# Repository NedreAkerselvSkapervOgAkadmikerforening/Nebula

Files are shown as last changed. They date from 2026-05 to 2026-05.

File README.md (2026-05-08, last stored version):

# Nebula
## Introduksjon
Nebula er foreningen NASAs neste generasjons flydatamaskin til bruk i foreningens modellrakketter.

## 🎯 Mål
1. Nebula skal være rask, kompakt, pålitelig, effektiv og enkel i bruk.
2. Nebula skal være bygd modulært, så nye sensorer og systemer kan innbyttes.
3. Sensorene i Nebula skal være nøyaktige og pålitelige.

## 💽 Oppbygning
Nebula kan overordnet deles i to kategorier:
1. Hovedkort
2. Modulene

### 🏠 Hovedkortet
Hovedkortet er hjernen og master i hele flydatamaskinen. Kortet bruker primært SPI-protokoll til å kommunisere med modulene.

Systemet drives av et enkelt 3.7 V LiPo-batteri, med 3.3 V logikk for alle moduler.

**Sensorer:**
- BMP390 - Trykk- og temperatursensor ([lenke](https://www.3achips.com/p/11139403?utm_source=octopart&utm_medium=cpc&utm_campaign=3achips_launch))
- BNO086 - Akselerometer, gyroskop og magnetometer

**Datalogging:**
- MEM2067-02-180-00-A - Hengslet SD kort modul ([lenke](https://no.mouser.com/ProductDetail/GCT/MEM2067-02-180-00-A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))

**Telemetri:**
- SX1276 - LoRa transceiver for trådløs kommunikasjon med bakken

**Kommunikasjon:**
- USB-C (alternativt micro USB) – for kommunikasjon med PC og programmering

**Strømforsyning:**
- Voltage divider - For å måle spenningen på batteriet gjennom ADC på mikrokontrolleren
- TPS63020 - 3.3V spenningsregulator (VURDER)
- JST 2-pin - For å koble til batteriet
- Power switch - For å slå av og på hele systemet

**Debugging:**
- Power LED - For å indikere at systemet er på
- Status LED - For å indikere systemstatus (f.eks. feil, normal drift, etc.)

### 📨 SPI
Hovedkortet fungerer som master, modulene som slaves. Hver modul har egen CS‑pin, som kan velges ved å lodde over riktig solder pad (CS1–CS6).

Mikrokontrolleren har totalt fire SPI-busser. 2 reserveres til selve hovedkortet, og 2 til modulene.

### 🖇️ Konnektorer
I alle moduler skal det være en 20 pin konnektor som kobler modulen til hovedkortet. Denne skal ha følgende pinout:
- CS: 6 stk
- MISO: 2 stk
- MOSI: 2 stk
- SCK: 2 stk
- 3vO: 1 stk
- GND: 1 stk
- GPIO: 6 stk

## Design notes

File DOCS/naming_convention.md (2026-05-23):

# Naming convention for nebula
Disse retningslinjene er ment for å sikre konsistens mellom moduler i PCB-design.

# Generelt
### 🐍 Alt bruker snakecase
altså_at_man_skriver_sånn_her

# Netlabels
### 📄 Netlabels skal være i formatet:
[modul(eks: "BNO086")][funksjon(eks: "MISO")][tiltegnet pin på MCU(eks: "30")]

### Eksempel
BNO086_MISO_30

### ⚡ Power
Alle positive powersymbols skal være 3.3V.

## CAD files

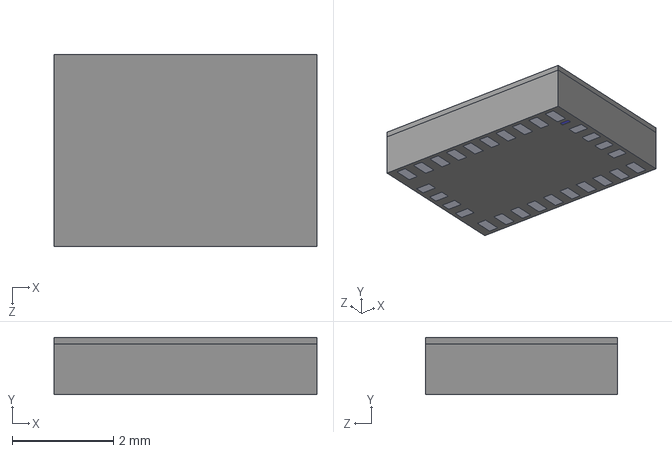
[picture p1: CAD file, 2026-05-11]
BNO086/DOCS/LIB_BNO086/BNO086/3D/BNO086.stp
5.20 x 1.13 x 3.80 mm

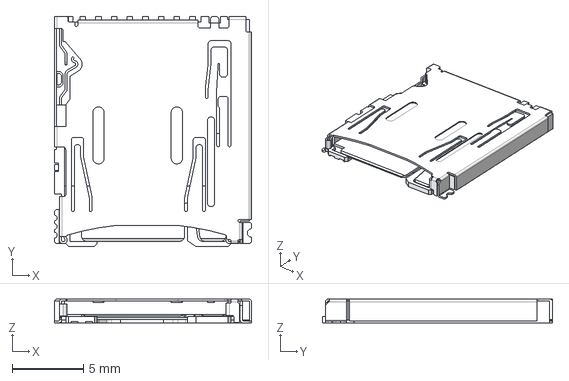
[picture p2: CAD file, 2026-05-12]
DM3AT/DM3AT_main/DM3AT-SF-PEJM5_40_.stp
13.8 x 16.2 x 1.68 mm

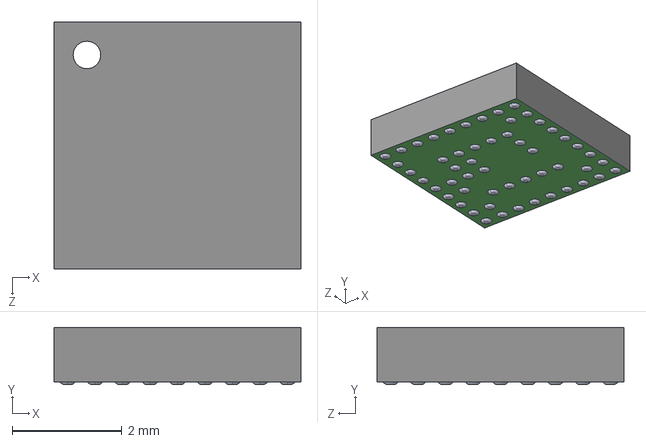
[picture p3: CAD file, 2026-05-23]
GPS pcb real/MIA-M10Q-00B feet/MIA-M10Q-00B.step
4.50 x 1.04 x 4.50 mm

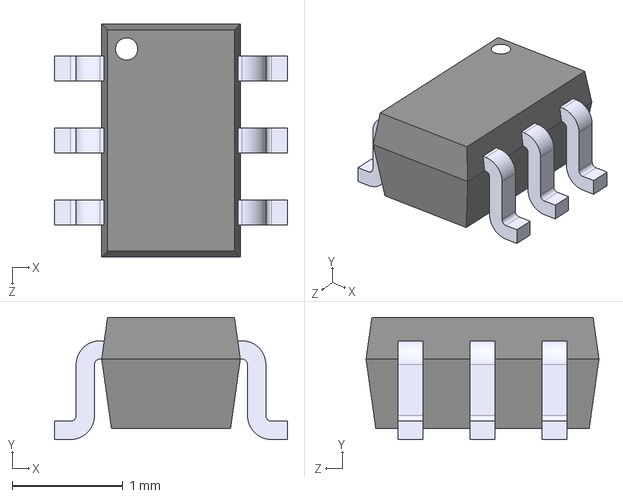
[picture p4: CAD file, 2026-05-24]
SX1276_Roy/PE4259/PE4259.step
2.10 x 1.10 x 2.10 mm

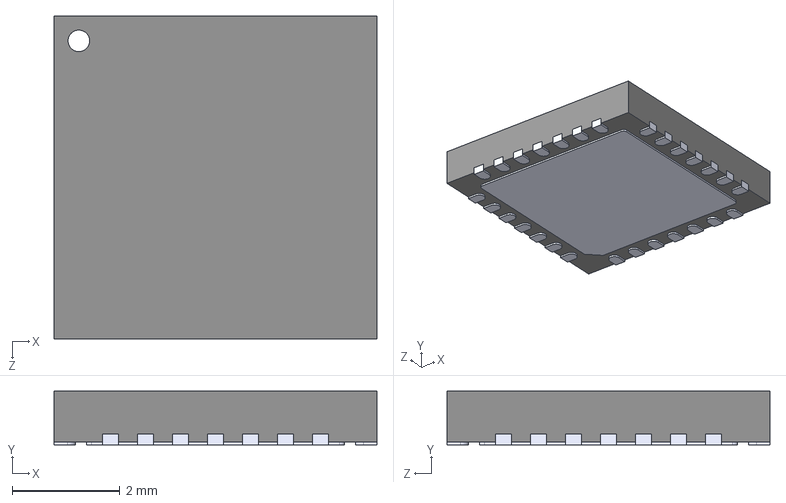
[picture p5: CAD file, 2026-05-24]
SX1276_Roy/SX1276IMLTRT/SX1276IMLTRT.step
6.00 x 1.00 x 6.00 mm

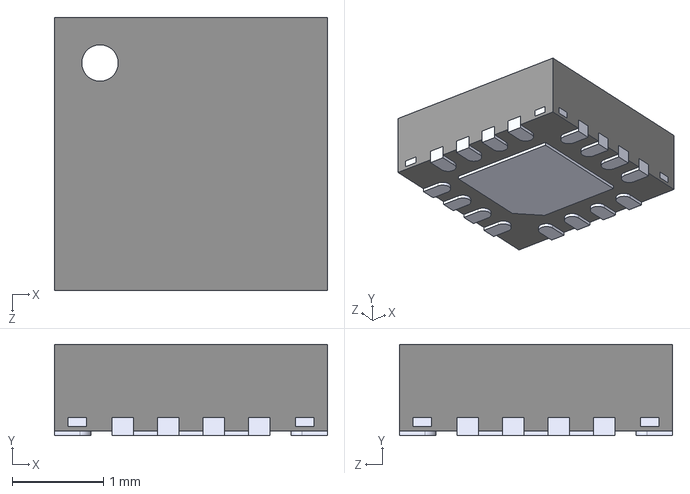
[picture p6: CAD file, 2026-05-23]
Batteri lader real/BQ24072RGTR feet/BQ24072RGTR.step
3.00 x 1.00 x 3.00 mm

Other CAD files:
BNO086/DOCS/LIB_BNO086/BNO086/Allegro/bno086.psm
BNO086/DOCS/LIB_BNO086/BNO086/DEHDL/bno086/chips/chips.prt

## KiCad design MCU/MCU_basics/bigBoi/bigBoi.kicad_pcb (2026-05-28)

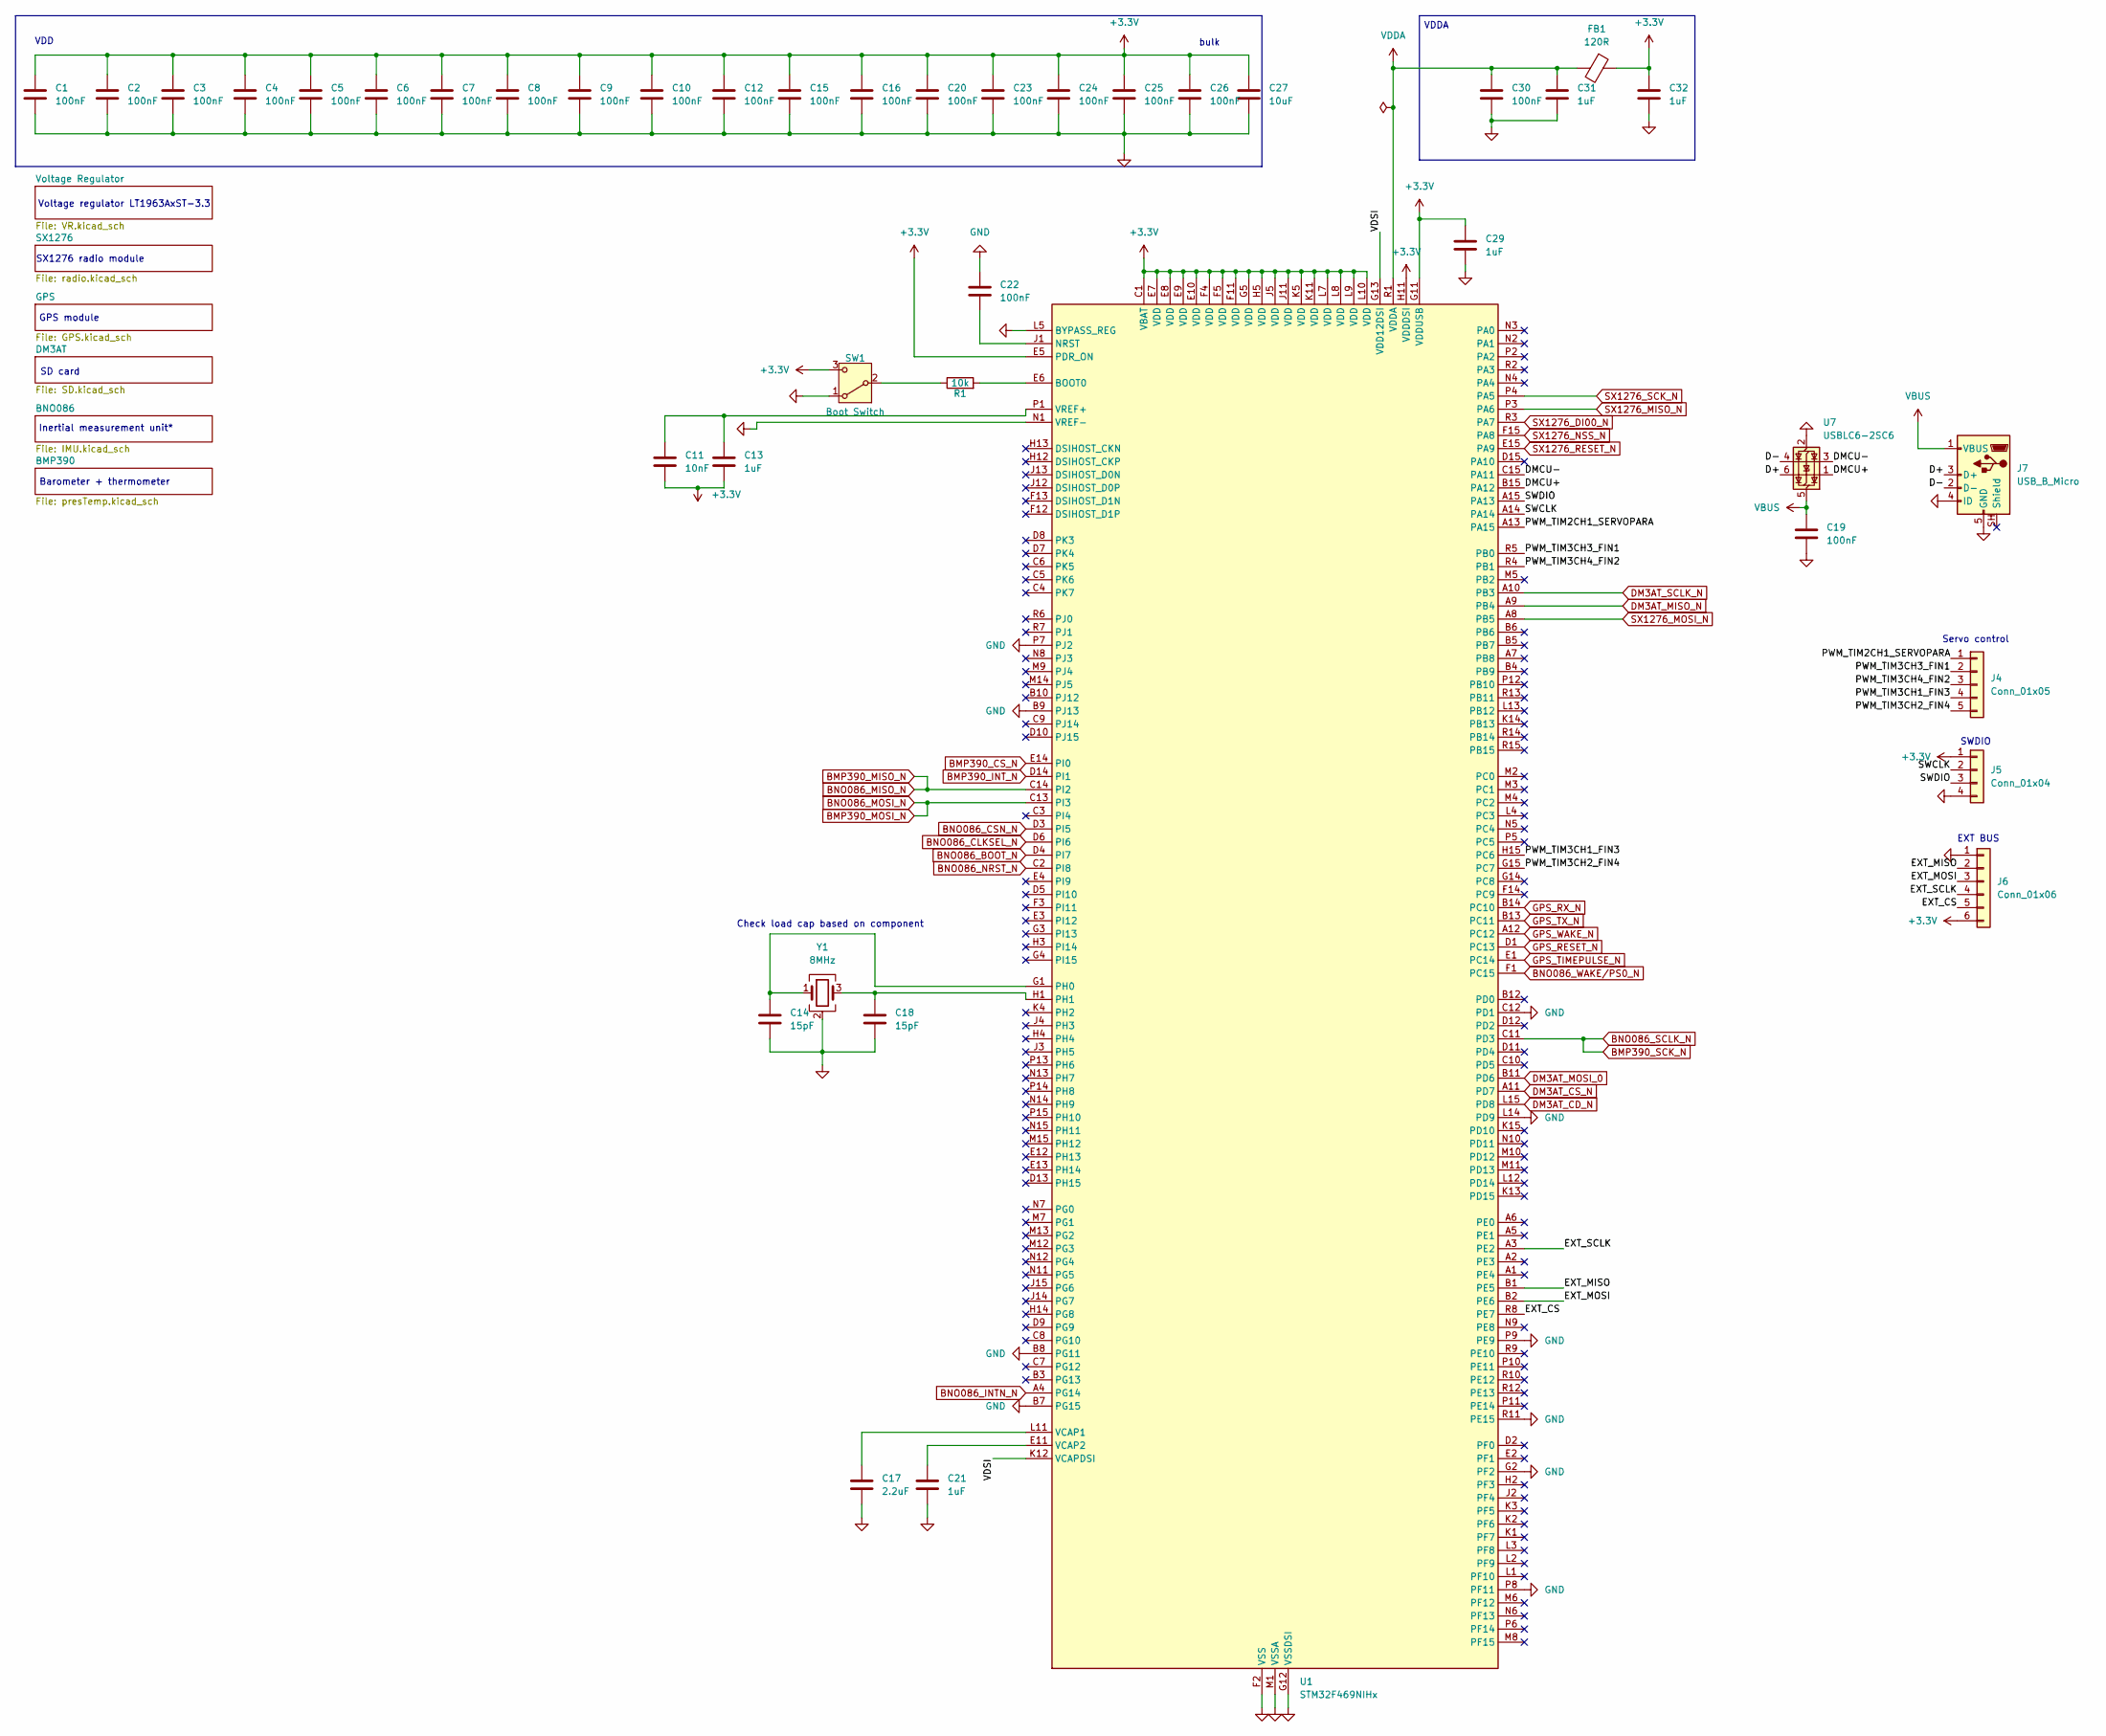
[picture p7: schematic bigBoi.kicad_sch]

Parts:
C1, C2, C3, C4, C5, C6, C7, C8, C9, C10, C12, C15, C16, C19, C20, C22, C23, C24, C25, C26, C30: 100nF; C_0402_1005Metric
C11: 10nF; C_0402_1005Metric
C13, C21, C29, C31, C32: 1uF; C_0402_1005Metric
C14, C18: 15pF; C_0402_1005Metric
C17: 2.2uF; C_0603_1608Metric
C27: 10uF; C_0805_2012Metric
FB1: 120R; L_0603_1608Metric
J4: Conn_01x05; PinHeader_1x05_P2.54mm_Vertical
J5: Conn_01x04; PinHeader_1x04_P2.54mm_Vertical
J6: Conn_01x06; PinHeader_1x06_P2.54mm_Vertical
J7: USB_B_Micro; USB_Micro-B_Molex_47346-0001
R1: 10k; R_0402_1005Metric
SW1: Boot Switch; SW_SPDT_PCM12
U1: STM32F469NIHx; TFBGA-216_13x13mm_Layout15x15_P0.8mm
U7: USBLC6-2SC6; SOT-23-6
Y1: 8MHz; Crystal_SMD_3225-4Pin_3.2x2.5mm

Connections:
+3.3V: C1.1, C2.1, C3.1, C4.1, C5.1, C6.1, C7.1, C8.1, C9.1, C10.1, C11.2, C12.1, C13.2, C15.1, C16.1, C20.1, C23.1, C24.1, C25.1, C26.1, C27.1, C29.1, C32.2, FB1.1, J5.1, J6.6, SW1.3 (C), U1.C1 (VBAT), U1.E5 (PDR_ON), U1.E7 (VDD), U1.E8 (VDD), U1.E9 (VDD), U1.E10 (VDD), U1.F4 (VDD), U1.F5 (VDD), U1.F11 (VDD), U1.G5 (VDD), U1.G11 (VDDUSB), U1.H5 (VDD), U1.H11 (VDDDSI), U1.J5 (VDD), U1.J11 (VDD), U1.K5 (VDD), U1.K11 (VDD), U1.L7 (VDD), U1.L8 (VDD), U1.L9 (VDD), U1.L10 (VDD); also elsewhere on the board
/D+: J7.3 (D+), U7.6 (I/O1)
/D-: J7.2 (D-), U7.4 (I/O2)
/DMCU+: U1.B15 (PA12), U7.1 (I/O1)
/DMCU-: U1.C15 (PA11), U7.3 (I/O2)
/EXT_CS: J6.5, U1.R8 (PE7)
/EXT_MISO: J6.2, U1.B1 (PE5)
/EXT_MOSI: J6.3, U1.B2 (PE6)
/EXT_SCLK: J6.4, U1.A3 (PE2)
/PWM_TIM2CH1_SERVOPARA: J4.1, U1.A13 (PA15)
/PWM_TIM3CH1_FIN3: J4.4, U1.H15 (PC6)
/PWM_TIM3CH2_FIN4: J4.5, U1.G15 (PC7)
/PWM_TIM3CH3_FIN1: J4.2, U1.R5 (PB0)
/PWM_TIM3CH4_FIN2: J4.3, U1.R4 (PB1)
/SWCLK: J5.2, U1.A14
/SWDIO: J5.3, U1.A15 (PA13)
/VDSI: U1.G13 (VDD12DSI), U1.K12 (VCAPDSI)
BMP390_CS_N: U1.E14 (PI0); also elsewhere on the board
BMP390_INT_N: U1.D14 (PI1); also elsewhere on the board
BMP390_MISO_N: U1.C14 (PI2); also elsewhere on the board
BMP390_MOSI_N: U1.C13 (PI3); also elsewhere on the board
BMP390_SCK_N: U1.C11 (PD3); also elsewhere on the board
BNO086_BOOT_N: U1.D4 (PI7); also elsewhere on the board
BNO086_CLKSEL_N: U1.D6 (PI6); also elsewhere on the board
BNO086_CSN_N: U1.D3 (PI5); also elsewhere on the board
BNO086_INTN_N: U1.A4 (PG14); also elsewhere on the board
BNO086_NRST_N: U1.C2 (PI8); also elsewhere on the board
BNO086_WAKE/PS0_N: U1.F1 (PC15); also elsewhere on the board
DM3AT_CD_N: U1.L15 (PD8); also elsewhere on the board
DM3AT_CS_N: U1.A11 (PD7); also elsewhere on the board
DM3AT_MISO_N: U1.A9 (PB4); also elsewhere on the board
DM3AT_MOSI_0: U1.B11 (PD6); also elsewhere on the board
DM3AT_SCLK_N: U1.A10 (PB3); also elsewhere on the board
GND: C1.2, C2.2, C3.2, C4.2, C5.2, C6.2, C7.2, C8.2, C9.2, C10.2, C12.2, C14.2, C15.2, C16.2, C17.2, C18.2, C19.2, C20.2, C21.1, C22.1, C23.2, C24.2, C25.2, C26.2, C27.2, C29.2, C30.1, C31.1, C32.1, J5.4, J6.1, J7.4 (ID), J7.5 (GND), SW1.1 (A), U1.B7 (PG15), U1.B8 (PG11), U1.B9 (PJ13), U1.C12 (PD1), U1.F2 (VSS), U1.F6 (VSS), U1.F7 (VSS), U1.F8 (VSS), U1.F9 (VSS), U1.F10 (VSS), U1.G2 (PF2), U1.G6 (VSS), U1.G10 (VSS), U1.G12 (VSSDSI), U1.H6 (VSS), U1.H10 (VSS), U1.J6 (VSS), U1.J10 (VSS), U1.K6 (VSS), U1.K7 (VSS), U1.K8 (VSS), U1.K9 (VSS), U1.K10 (VSS), U1.L5 (BYPASS_REG), U1.L6 (VSS), U1.L14 (PD9), U1.M1 (VSSA), U1.N1 (VREF-), U1.P7 (PJ2), U1.P8 (PF11), U1.P9 (PE9), U1.R11 (PE15), U7.2 (GND), Y1.2 (G), Y1.4 (G); also elsewhere on the board
GPS_RESET_N: U1.D1 (PC13); also elsewhere on the board
GPS_RX_N: U1.B14 (PC10); also elsewhere on the board
GPS_TIMEPULSE_N: U1.E1 (PC14); also elsewhere on the board
GPS_TX_N: U1.B13 (PC11); also elsewhere on the board
GPS_WAKE_N: U1.A12 (PC12); also elsewhere on the board
unnamed: R1.1, SW1.2 (B)
unnamed: R1.2, U1.E6 (BOOT0)
unnamed: C22.2, U1.J1 (NRST)
unnamed: C14.1, U1.G1 (PH0), Y1.1
unnamed: C18.1, U1.H1, Y1.3
unnamed: C17.1, U1.L11 (VCAP1)
unnamed: C21.2, U1.E11 (VCAP2)
unnamed: C11.1, C13.1, U1.P1 (VREF+)
SX1276_DI00_N: U1.R3 (PA7); also elsewhere on the board
SX1276_MISO_N: U1.P3 (PA6); also elsewhere on the board
SX1276_MOSI_N: U1.A8 (PB5); also elsewhere on the board
SX1276_NSS_N: U1.F15 (PA8); also elsewhere on the board
SX1276_RESET_N: U1.E15 (PA9); also elsewhere on the board
SX1276_SCK_N: U1.P4 (PA5); also elsewhere on the board
VBUS: C19.1, J7.1 (VBUS), U7.5 (VBUS); also elsewhere on the board
VDDA: C30.2, C31.2, FB1.2, U1.R1 (VDDA)

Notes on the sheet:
Inertial measurement unit*
bulk
VDD
EXT BUS
GPS module
SD card
VDDA
Voltage regulator LT1963AxST-3.3
Check load cap based on component
SX1276 radio module
Barometer + thermometer
SWDIO
Servo control

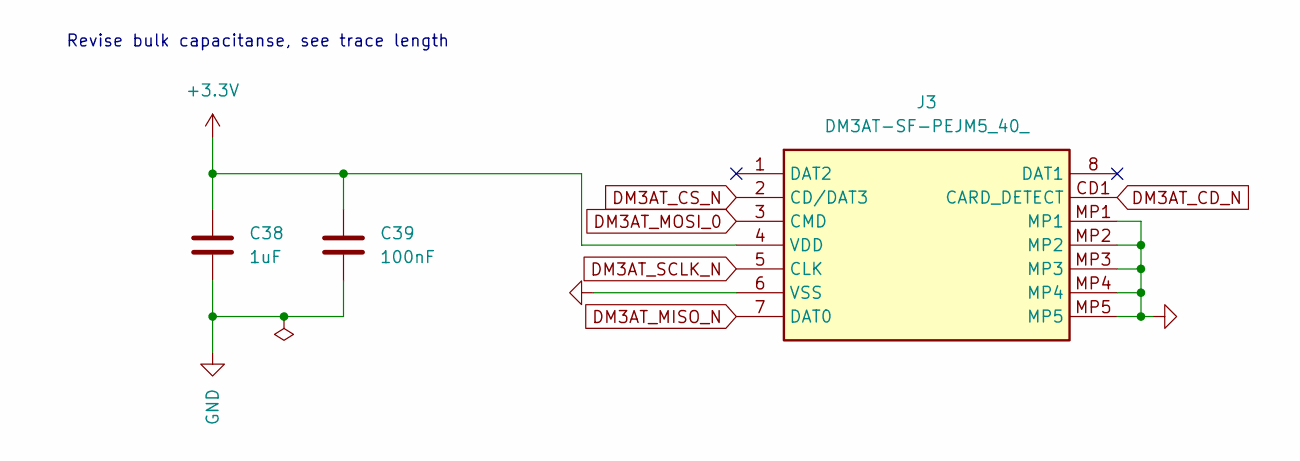
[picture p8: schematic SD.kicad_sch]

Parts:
C38: 1uF; C_0402_1005Metric
C39: 100nF; C_0402_1005Metric
J3: DM3AT-SF-PEJM5_40_; DM3ATSFPEJM540; Mouser Part Number 798-DM3AT-SF-PEJM540

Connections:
+3.3V: C38.1, C39.1, J3.4 (VDD); also elsewhere on the board
DM3AT_CD_N: J3.CD1 (CARD_DETECT); also elsewhere on the board
DM3AT_CS_N: J3.2 (CD/DAT3); also elsewhere on the board
DM3AT_MISO_N: J3.7 (DAT0); also elsewhere on the board
DM3AT_MOSI_0: J3.3 (CMD); also elsewhere on the board
DM3AT_SCLK_N: J3.5 (CLK); also elsewhere on the board
GND: C38.2, C39.2, J3.6 (VSS), J3.MP1, J3.MP2, J3.MP3, J3.MP4, J3.MP5; also elsewhere on the board

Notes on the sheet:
Revise bulk capacitanse, see trace length

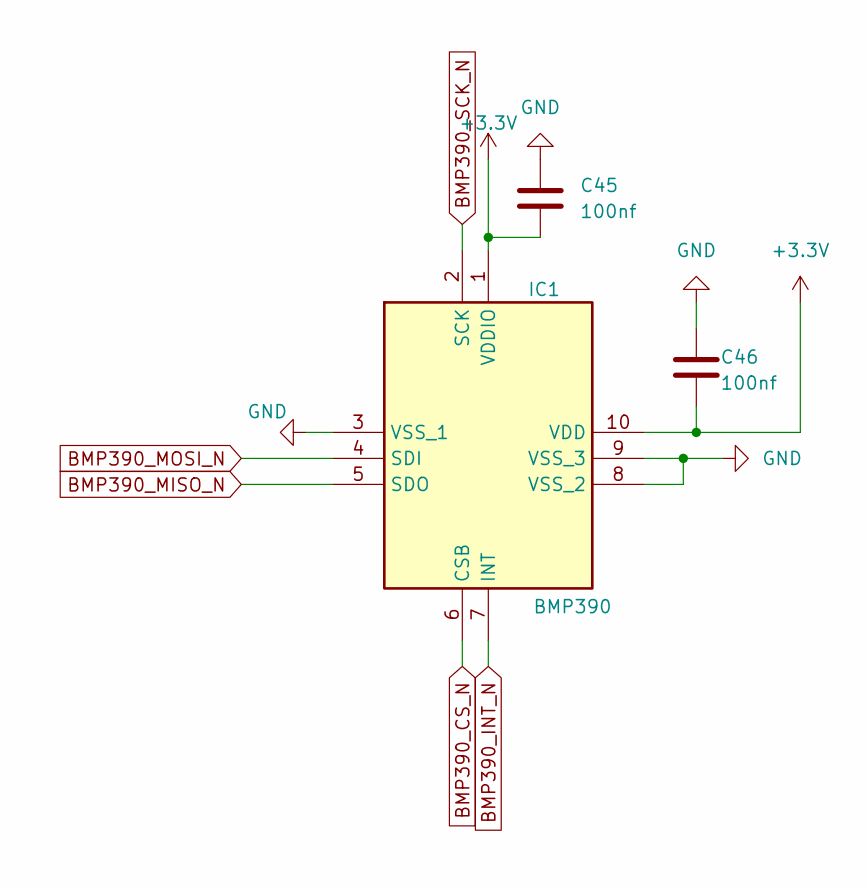
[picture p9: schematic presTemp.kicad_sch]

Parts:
C45, C46: 100nf; C_0402_1005Metric
IC1: BMP390; Manufacturer_Part_Number BMP390; Mouser Part Number 262-BMP390

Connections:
+3.3V: C45.2, C46.2, IC1.1 (VDDIO), IC1.10 (VDD); also elsewhere on the board
BMP390_CS_N: IC1.6 (CSB); also elsewhere on the board
BMP390_INT_N: IC1.7 (INT); also elsewhere on the board
BMP390_MISO_N: IC1.5 (SDO); also elsewhere on the board
BMP390_MOSI_N: IC1.4 (SDI); also elsewhere on the board
BMP390_SCK_N: IC1.2 (SCK); also elsewhere on the board
GND: C45.1, C46.1, IC1.3 (VSS_1), IC1.8 (VSS_2), IC1.9 (VSS_3); also elsewhere on the board

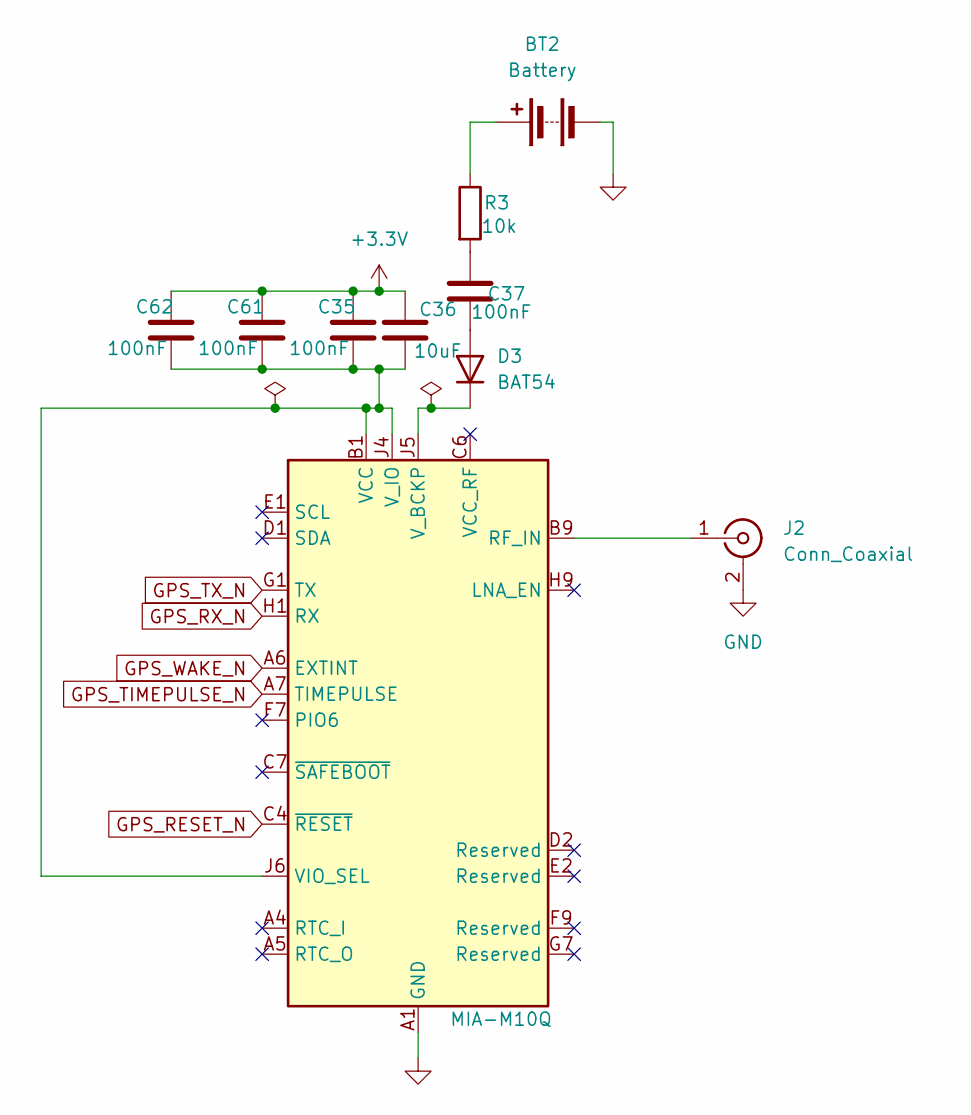
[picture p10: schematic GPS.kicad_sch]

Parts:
BT2: Battery; BatteryHolder_LINX_BAT-HLD-012-SMT
C35, C37, C61, C62: 100nF; C_0402_1005Metric
C36: 10uF; C_0603_1608Metric
D3: BAT54; D_0402_1005Metric
J2: Conn_Coaxial; U.FL_Hirose_U.FL-R-SMT-1_Vertical
R3: 10k; R_0402_1005Metric
U5: MIA-M10Q

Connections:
+3.3V: C35.1, C36.1, C61.1, C62.1; also elsewhere on the board
GND: BT2.2 (-), J2.2 (Ext), U5.A1 (GND), U5.A2 (GND), U5.A3 (GND), U5.A8 (GND), U5.A9 (GND), U5.B2 (GND), U5.B8 (GND), U5.C3 (GND), U5.C9 (GND), U5.E3 (GND), U5.E4 (GND), U5.E9 (GND), U5.F1 (GND), U5.F3 (GND), U5.F4 (GND), U5.G3 (GND), U5.G4 (GND), U5.G5 (GND), U5.G6 (GND), U5.H8 (GND), U5.J8 (GND), U5.J9 (GND); also elsewhere on the board
GPS_RESET_N: U5.C4 (~RESET); also elsewhere on the board
GPS_RX_N: U5.H1 (RX); also elsewhere on the board
GPS_TIMEPULSE_N: U5.A7 (TIMEPULSE); also elsewhere on the board
GPS_TX_N: U5.G1 (TX); also elsewhere on the board
GPS_WAKE_N: U5.A6 (EXTINT); also elsewhere on the board
unnamed: BT2.1 (+), R3.1
unnamed: C37.2, R3.2
unnamed: C37.1, D3.2 (A)
unnamed: D3.1 (K), U5.J5 (V_BCKP)
unnamed: J2.1 (In), U5.B9 (RF_IN)
unnamed: C35.2, C36.2, C61.2, C62.2, U5.B1 (VCC), U5.J4 (V_IO), U5.J6 (VIO_SEL)

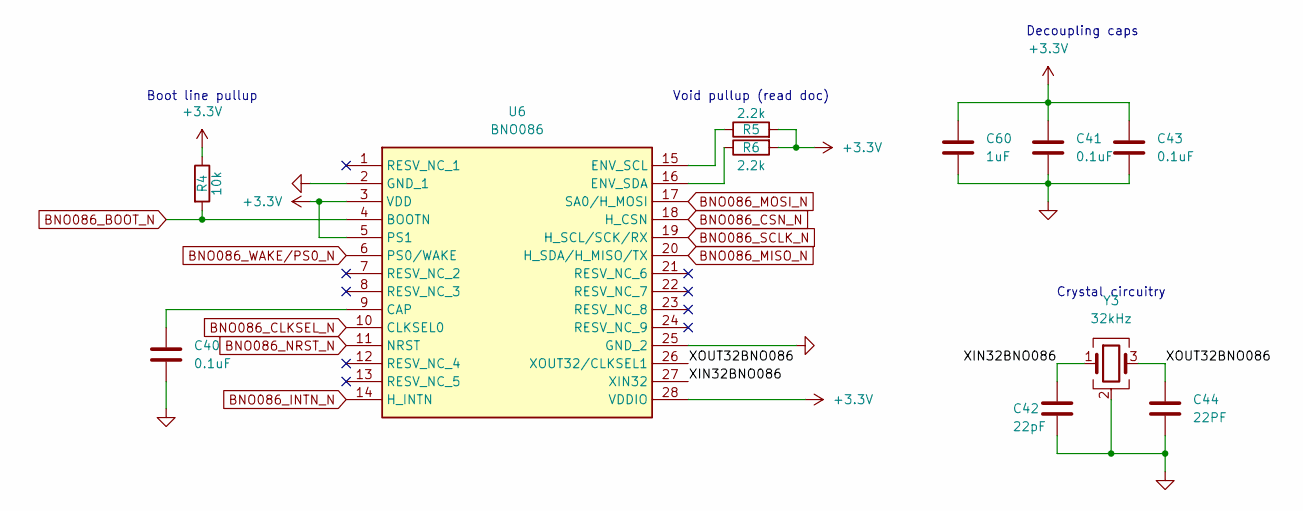
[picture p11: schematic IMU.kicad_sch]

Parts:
C40, C41, C43: 0.1uF; C_0402_1005Metric
C42: 22pF; C_0402_1005Metric
C44: 22PF; C_0402_1005Metric
C60: 1uF; C_0402_1005Metric
R4: 10k; R_0402_1005Metric
R5, R6: 2.2k; R_0402_1005Metric
U6: BNO086; Mouser Part Number 526-BNO086
Y3: 32kHz; Crystal_SMD_3225-4Pin_3.2x2.5mm

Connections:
+3.3V: C41.1, C43.1, C60.1, R4.1, R5.2, R6.2, U6.3 (VDD), U6.5 (PS1), U6.28 (VDDIO); also elsewhere on the board
/BNO086/XIN32BNO086: C42.1, U6.27 (XIN32), Y3.1
/BNO086/XOUT32BNO086: C44.1, U6.26 (XOUT32/CLKSEL1), Y3.3
BMP390_MISO_N: U6.20 (H_SDA/H_MISO/TX); also elsewhere on the board
BMP390_MOSI_N: U6.17 (SA0/H_MOSI); also elsewhere on the board
BMP390_SCK_N: U6.19 (H_SCL/SCK/RX); also elsewhere on the board
BNO086_BOOT_N: R4.2, U6.4 (BOOTN); also elsewhere on the board
BNO086_CLKSEL_N: U6.10 (CLKSEL0); also elsewhere on the board
BNO086_CSN_N: U6.18 (H_CSN); also elsewhere on the board
BNO086_INTN_N: U6.14 (H_INTN); also elsewhere on the board
BNO086_NRST_N: U6.11 (NRST); also elsewhere on the board
BNO086_WAKE/PS0_N: U6.6 (PS0/WAKE); also elsewhere on the board
GND: C40.2, C41.2, C42.2, C43.2, C44.2, C60.2, U6.2 (GND_1), U6.25 (GND_2), Y3.2 (G), Y3.4 (G); also elsewhere on the board
unnamed: C40.1, U6.9 (CAP)
unnamed: R5.1, U6.15 (ENV_SCL)
unnamed: R6.1, U6.16 (ENV_SDA)

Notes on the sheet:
Boot line pullup
Decoupling caps
Void pullup (read doc)
Crystal circuitry

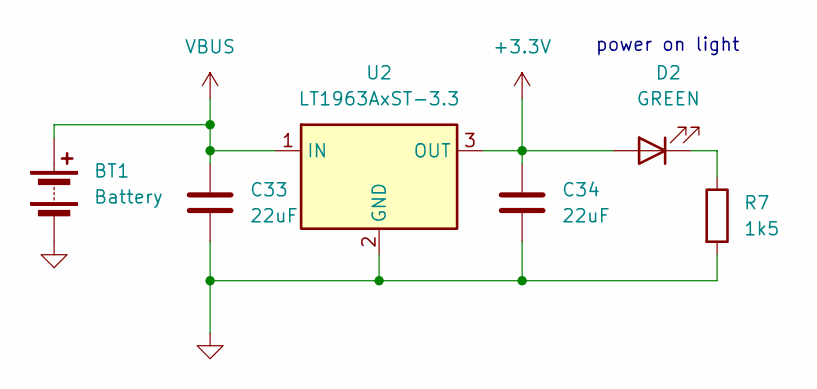
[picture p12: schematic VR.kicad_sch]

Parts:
BT1: Battery; JST_PH_S2B-PH-K_1x02_P2.00mm_Horizontal
C33, C34: 22uF; C_0805_2012Metric
D2: GREEN; LED_0603_1608Metric
R7: 1k5; R_0402_1005Metric
U2: LT1963AxST-3.3; SOT-223-3_TabPin2

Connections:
+3.3V: C34.1, D2.2 (A), U2.3 (OUT); also elsewhere on the board
GND: BT1.2 (-), C33.2, C34.2, R7.2, U2.2 (GND); also elsewhere on the board
unnamed: D2.1 (K), R7.1
VBUS: BT1.1 (+), C33.1, U2.1 (IN); also elsewhere on the board

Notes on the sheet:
power on light

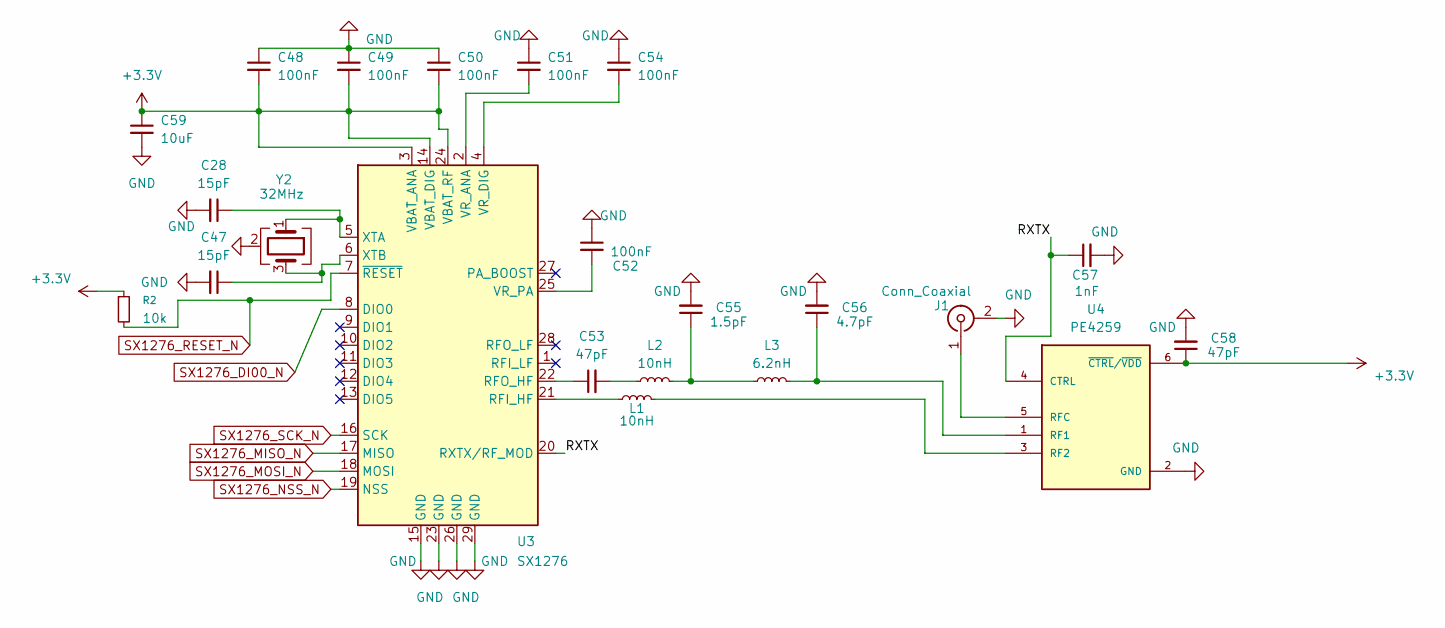
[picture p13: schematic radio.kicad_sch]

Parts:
C28, C47: 15pF; C_0402_1005Metric
C48, C49, C50, C51, C52, C54: 100nF; C_0402_1005Metric
C53, C58: 47pF; C_0402_1005Metric
C55: 1.5pF; C_0402_1005Metric
C56: 4.7pF; C_0402_1005Metric
C57: 1nF; C_0402_1005Metric
C59: 10uF; C_0805_2012Metric
J1: Conn_Coaxial; U.FL_Hirose_U.FL-R-SMT-1_Vertical
L1, L2: 10nH; L_0402_1005Metric
L3: 6.2nH; L_0402_1005Metric
R2: 10k; R_0402_1005Metric
U3: SX1276; QFN65P600X600X100-29N
U4: PE4259; SOT65P215X110-6N
Y2: 32MHz; Crystal_SMD_3225-4Pin_3.2x2.5mm

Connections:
+3.3V: C48.2, C49.2, C50.2, C58.1, C59.1, R2.1, U3.3 (VBAT_ANA), U3.14 (VBAT_DIG), U3.24 (VBAT_RF), U4.6 (~CTRL/~VDD); also elsewhere on the board
/SX1276/RXTX: C57.1, U3.20 (RXTX/RF_MOD), U4.4 (CTRL)
GND: C28.2, C47.2, C48.1, C49.1, C50.1, C51.1, C52.1, C54.1, C55.2, C56.2, C57.2, C58.2, C59.2, J1.2 (Ext), U3.15 (GND), U3.23 (GND), U3.26 (GND), U3.29 (GND), U4.2 (GND), Y2.2 (G), Y2.4 (G); also elsewhere on the board
unnamed: C53.2, L2.1
unnamed: C55.1, L2.2, L3.1
unnamed: J1.1 (In), U4.5 (RFC)
unnamed: L1.1, U3.21 (RFI_HF)
unnamed: C53.1, U3.22 (RFO_HF)
unnamed: C51.2, U3.2 (VR_ANA)
unnamed: C54.2, U3.4 (VR_DIG)
unnamed: C52.2, U3.25 (VR_PA)
unnamed: C28.1, U3.5 (XTA), Y2.1
unnamed: C47.1, U3.6 (XTB), Y2.3
unnamed: C56.1, L3.2, U4.1 (RF1)
unnamed: L1.2, U4.3 (RF2)
SX1276_DI00_N: U3.8 (DIO0); also elsewhere on the board
SX1276_MISO_N: U3.17 (MISO); also elsewhere on the board
SX1276_MOSI_N: U3.18 (MOSI); also elsewhere on the board
SX1276_NSS_N: U3.19 (NSS); also elsewhere on the board
SX1276_RESET_N: R2.2, U3.7 (~RESET); also elsewhere on the board
SX1276_SCK_N: U3.16 (SCK); also elsewhere on the board

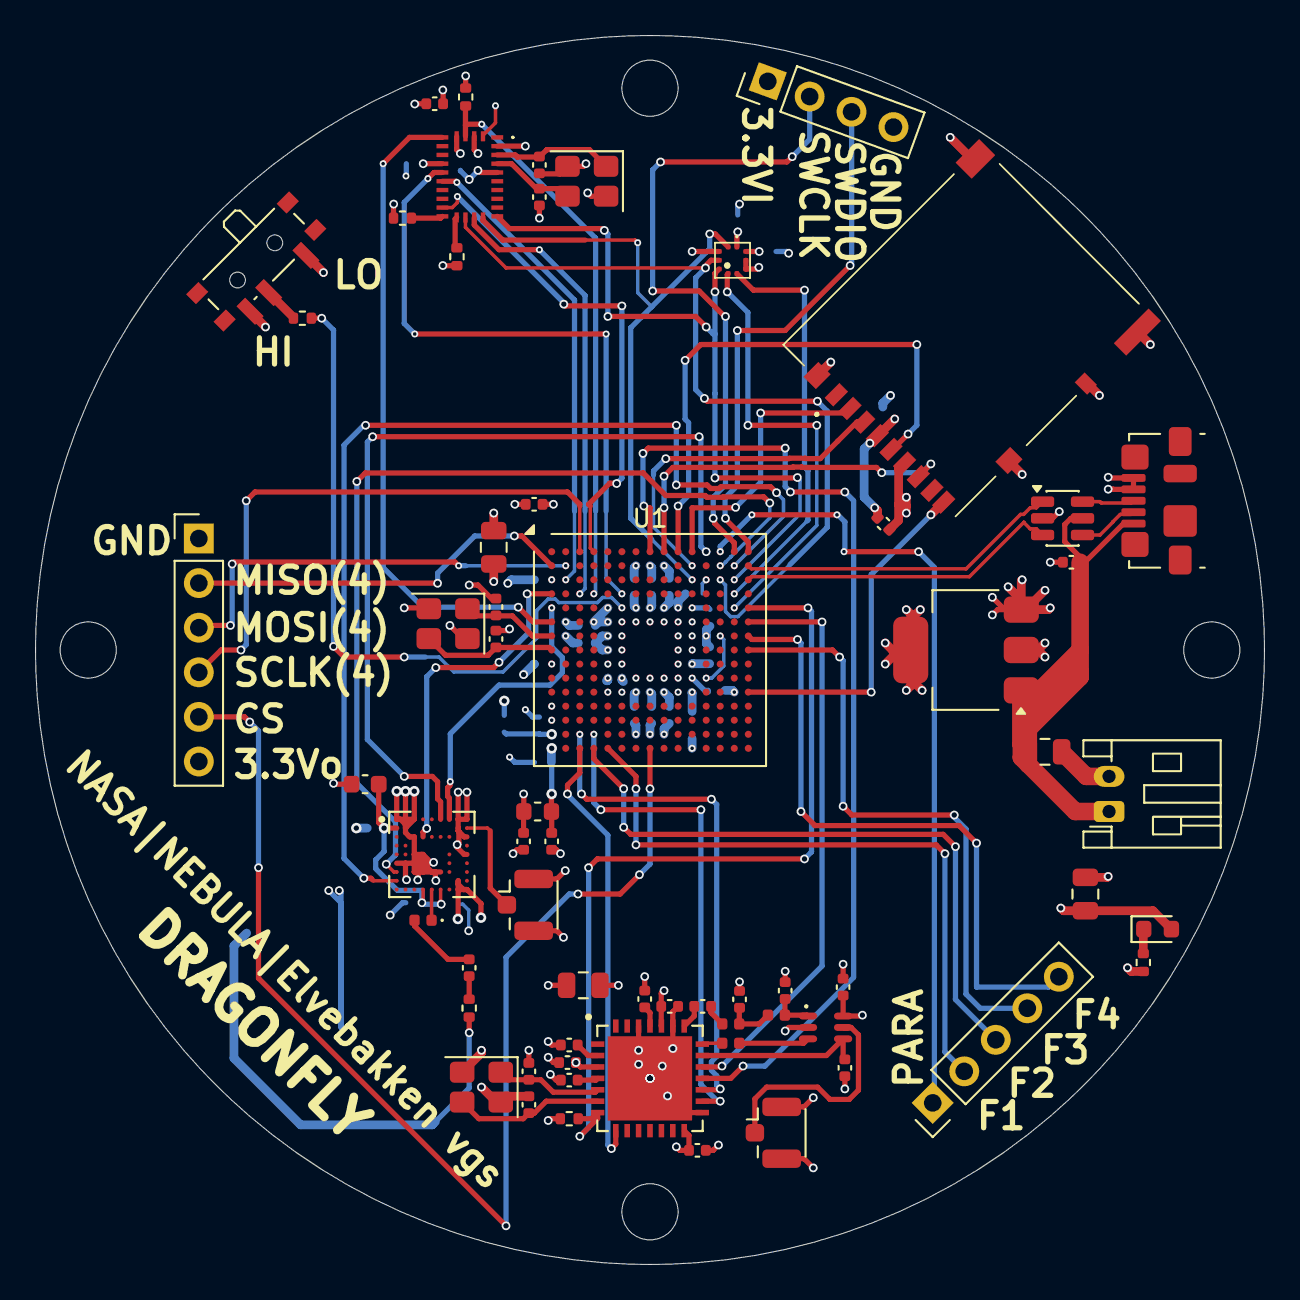
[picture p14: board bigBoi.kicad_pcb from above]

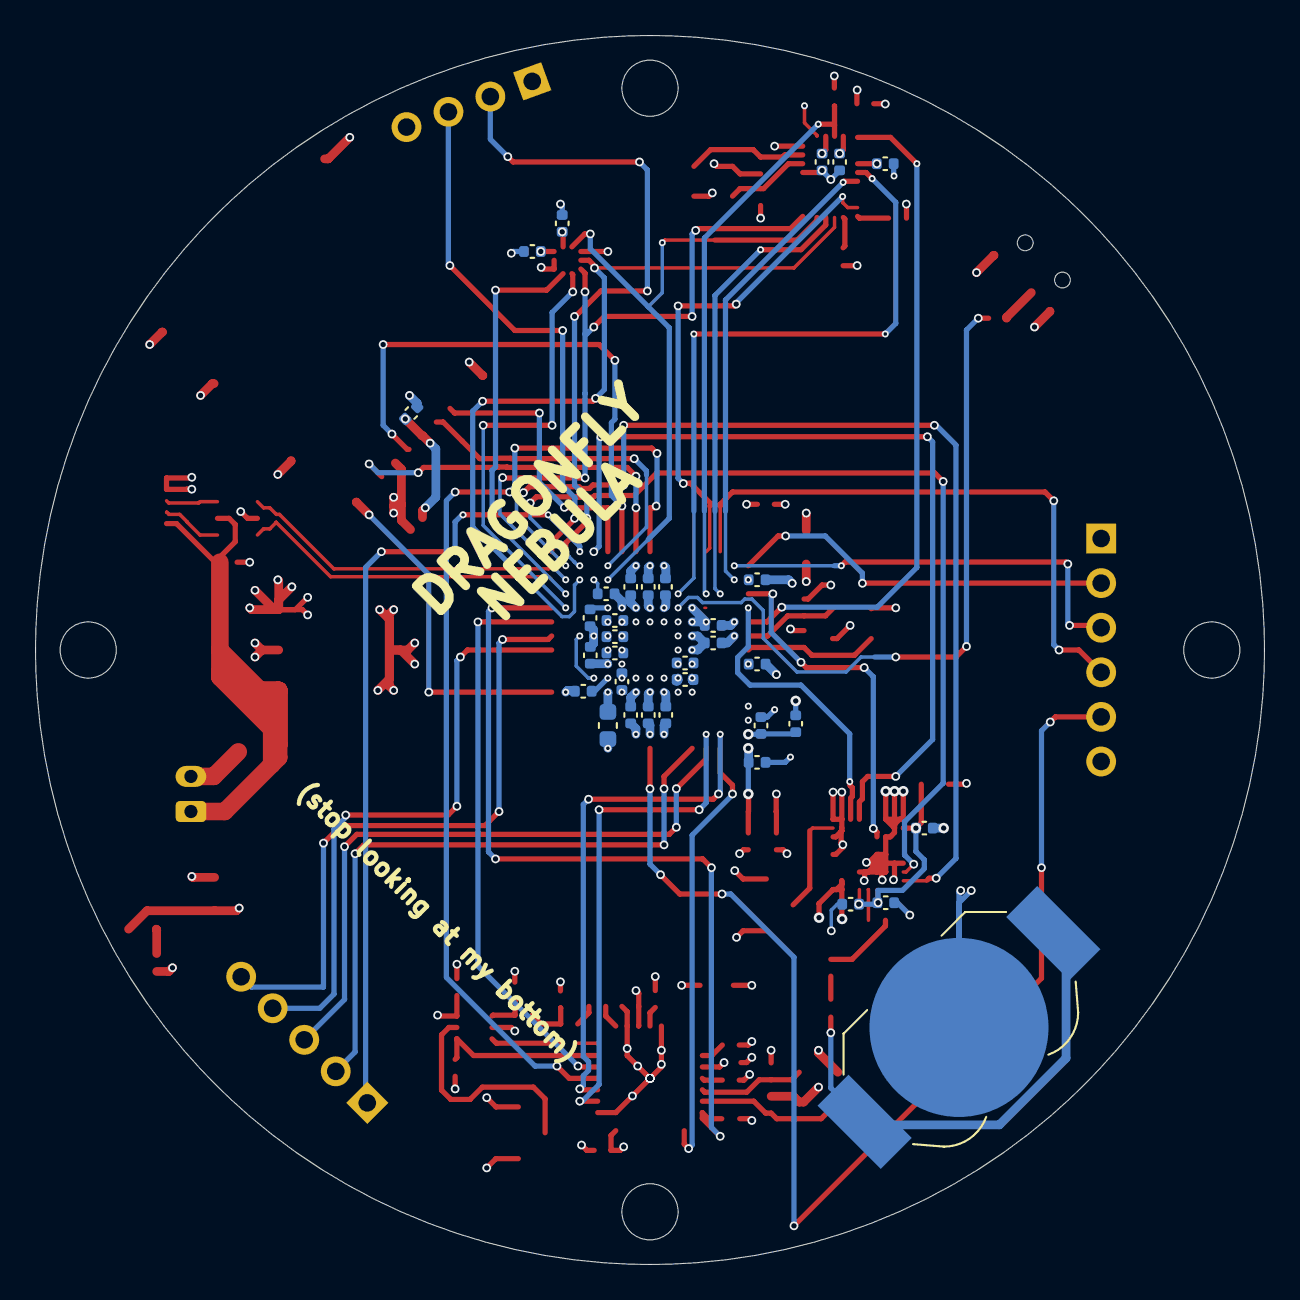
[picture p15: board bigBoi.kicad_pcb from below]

Board: 4 copper layers, 70.0 x 70.0 mm, 96 parts (34 on the bottom side), 80 nets.

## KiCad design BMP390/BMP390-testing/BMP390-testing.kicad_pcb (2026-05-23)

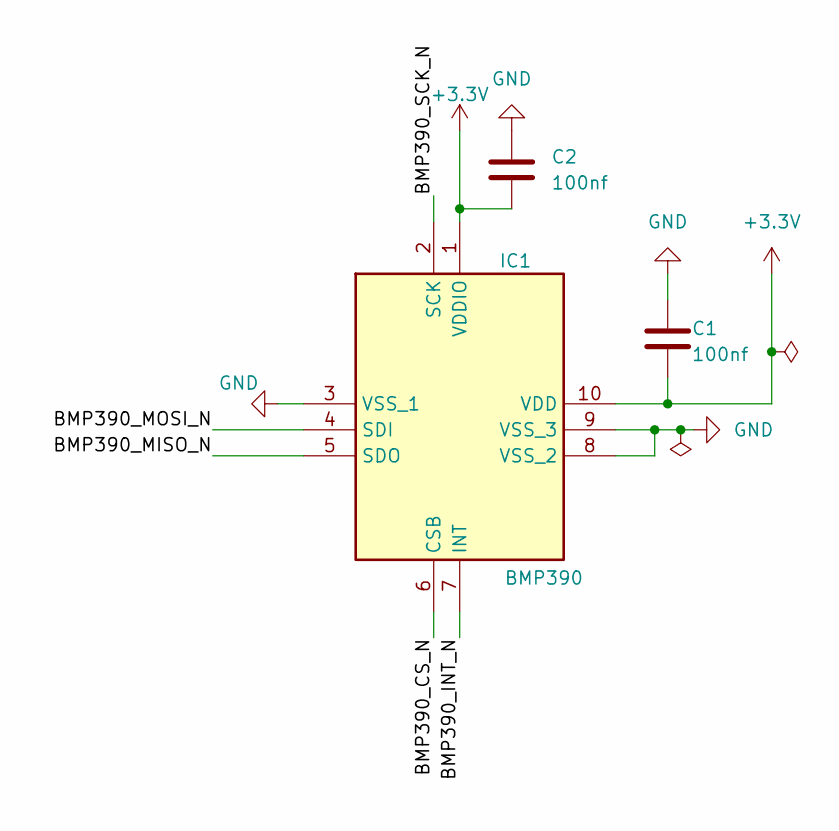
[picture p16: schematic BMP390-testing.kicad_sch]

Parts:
C1, C2: 100nf; C_0402_1005Metric
IC1: BMP390; Manufacturer_Part_Number BMP390; Mouser Part Number 262-BMP390

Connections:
+3V3: C1.2, C2.2, IC1.1 (VDDIO), IC1.10 (VDD)
/CS: IC1.6 (CSB)
/INT: IC1.7 (INT)
/MISO: IC1.5 (SDO)
/MOSI: IC1.4 (SDI)
/SCK: IC1.2 (SCK)
GND: C1.1, C2.1, IC1.3 (VSS_1), IC1.8 (VSS_2), IC1.9 (VSS_3)

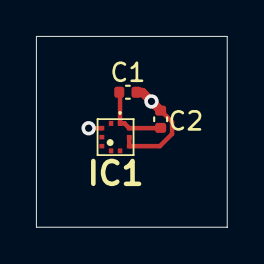
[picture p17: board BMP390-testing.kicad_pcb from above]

Board: 4 copper layers, 10.6 x 10.6 mm, 3 parts (0 on the bottom side), 2 nets.

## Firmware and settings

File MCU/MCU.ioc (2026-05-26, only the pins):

Mcu.UserName=STM32F469NIHx
PA11.Signal=USB_OTG_FS_DM
PA12.Signal=USB_OTG_FS_DP
PA13.Signal=SYS_JTMS-SWDIO
PA14.Signal=SYS_JTCK-SWCLK
PA15.Signal=S_TIM2_CH1_ETR
PA5.Signal=SPI1_SCK
PA6.Signal=SPI1_MISO
PA7.Signal=GPXTI7
PA8.Signal=GPIO_Output
PA9.Signal=GPIO_Output
PB0.Signal=S_TIM3_CH3
PB1.Signal=S_TIM3_CH4
PB3.Signal=SPI3_SCK
PB4.Signal=SPI3_MISO
PB5.Signal=SPI1_MOSI
PC10.Signal=UART4_TX
PC11.Signal=UART4_RX
PC12.Signal=GPIO_Output
PC13.Signal=GPIO_Output
PC15/OSC32_OUT.Signal=GPXTI15
PC6.Signal=S_TIM3_CH1
PC7.Signal=S_TIM3_CH2
PD3.Signal=SPI2_SCK
PD6.Signal=SPI3_MOSI
PD7.Signal=GPIO_Output
PD8.Signal=GPIO_Output
PE2.Signal=SPI4_SCK
PE5.Signal=SPI4_MISO
PE6.Signal=SPI4_MOSI
PE7.Signal=GPIO_Output
PG14.Signal=GPXTI14
PH0/OSC_IN.Signal=RCC_OSC_IN
PH1/OSC_OUT.Signal=RCC_OSC_OUT
PI0.Signal=GPIO_Output
PI1.Signal=GPXTI1
PI2.Signal=SPI2_MISO
PI3.Signal=SPI2_MOSI
PI5.Signal=GPIO_Output
PI6.Signal=GPIO_Output
PI7.Signal=GPIO_Output
PI8.Signal=GPIO_Output

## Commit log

2026-04-02 Footprint start
    [nebula_fp.kicad_pcb, nebula_fp.kicad_sch]
2026-04-13 gps schematic
2026-04-27 John Fix Move Lader
    [batteri lader pcb.kicad_pcb, batteri lader pcb.kicad_sch]
2026-04-27 GPS locked in
    [gps pcb.kicad_pcb, gps pcb.kicad_sch]
2026-05-11 BNO086 schematic
    [BNO086.stp, BNO086_main.kicad_pcb, BNO086_main.kicad_sch]
2026-05-11 Schematic doc
2026-05-13 Should be SD
    [DM3AT_main.kicad_sch]
2026-05-13 start MCU power circuit
    [DM3AT_main.kicad_sch, bigBoi.kicad_pcb, bigBoi.kicad_sch]
2026-05-15 Power rails routed
    [VR.kicad_sch, bigBoi.kicad_sch]
2026-05-15 Rename stuff for Main Chip
    [SX1276.kicad_pcb, SX1276.kicad_sch]
2026-05-15 fiksa filsystemer (ish)
    [gps pcb.kicad_pcb, gps pcb.kicad_sch, servo.controler.kicad_pcb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]
2026-05-15 MCU small update
    [bigBoi.kicad_sch, radio.kicad_sch]
2026-05-20 more power basics and comm
    [GPS.kicad_sch, IMU.kicad_sch, SD.kicad_sch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]
2026-05-21 BMP390 test
    [BMP390-testing.kicad_pcb, BMP390-testing.kicad_sch]
2026-05-21 BMP390 oppdatert til å følge naming convention
    [BMP390-testing.kicad_sch]
2026-05-21 Litt mer naming convention, la den til tilbake johannes 👀👀
2026-05-22 Schematic pins assignment
    [GPS.kicad_sch, bigBoi.kicad_sch, radio.kicad_sch]
2026-05-22 schematic connections
    [GPS.kicad_sch, IMU.kicad_sch, VR.kicad_sch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]
2026-05-23 ERC resolving
    [GPS.kicad_sch, IMU.kicad_sch, SD.kicad_sch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]
2026-05-23 ERC hierarchical labeling solved
    [bigBoi.kicad_sch, presTemp.kicad_sch]
2026-05-23 fiksa og triksa lit
    [batteri lader pcb.kicad_sch, gps pcb.kicad_sch]
2026-05-23 most footprints assigned
    [GPS.kicad_sch, bigBoi.kicad_pcb, bigBoi.kicad_sch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]
2026-05-23 update nebula FP
    [bigBoi.kicad_pcb, nebula_fp.kicad_pcb]
2026-05-23 La til footprints
2026-05-24 small changes
    [GPS.kicad_sch, bigBoi.kicad_pcb, presTemp.kicad_sch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]
2026-05-24 Lokale Footprints
    [PE4259.step, SX1276IMLTRT.step]
2026-05-24 Y2 fixed
    [GPS.kicad_sch, bigBoi.kicad_sch, presTemp.kicad_sch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]
2026-05-24 footprints assigned
    [presTemp.kicad_sch, radio.kicad_sch]
2026-05-26 Via escape routing
    [bigBoi.kicad_pcb]
2026-05-26 decoupling cap placement
    [SD.kicad_sch, bigBoi.kicad_pcb, bigBoi.kicad_sch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]
2026-05-26 MCU pwr+esc
    [bigBoi.kicad_pcb, bigBoi.kicad_sch, presTemp.kicad_sch]
2026-05-26 Store deler av VBUS og USB
    [IMU.kicad_sch, bigBoi.kicad_pcb, bigBoi.kicad_sch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]
2026-05-26 Layout kategorier
    [SD.kicad_sch, bigBoi.kicad_pcb, presTemp.kicad_sch]
2026-05-27 SX1276 layout
    [IMU.kicad_sch, bigBoi.kicad_pcb, bigBoi.kicad_sch]
2026-05-28 routing complete
    [GPS.kicad_sch, IMU.kicad_sch, bigBoi.kicad_pcb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]
